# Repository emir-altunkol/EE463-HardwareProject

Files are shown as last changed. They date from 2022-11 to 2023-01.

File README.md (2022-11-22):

# EE463-HardwareProject

This is a repository for the term project of the EE463 Static Power Conversion I course given by METU EEE department. It is a DC motor drive project, whose details are included in the [course repository](https://github.com/odtu/ee463).

## Team Members (Hard-Time Regulators): 

* Işık Emir Altunkol
* Fatih Erden
* İsmail Macit

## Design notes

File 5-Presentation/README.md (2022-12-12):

## Component List

The spreadsheet link for the current state of the component list is given [here](https://docs.google.com/spreadsheets/d/14lQKjTt1QYeIo84nUDRivLAAxynFq0hbY2szFumdkH8/edit?usp=sharing).

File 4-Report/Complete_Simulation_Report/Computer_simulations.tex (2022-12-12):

\section{Computer Simulations} \label{simulations}

\subsection{LTspice Simulations}
Since the 4-quadrant operation and control of the H-Bridge topology is not simple, we made comprehensive simulations using LTspice.A brief description of those and their results will be explained in this subsection. First, the simulation model will be described. \\

The model for the topology we are using is given in Figure \ref{fig:LTspice_topology_sch}. MOSFET models are chosen from the libraries of LTspice, whose ratings are compatible with our operation ranges. To simulate the rectified DC voltage on the input side, we occasionally used an ideal DC source to simplify the results by avoiding the input voltage ripple. We used a diode to model the one-directional current flow of the rectifier, and a capacitor to model the output filtering capacitor of the rectifier. The chopper and the H-Bridge is model is rather straightforward.

\begin{figure}[H]
    \centering
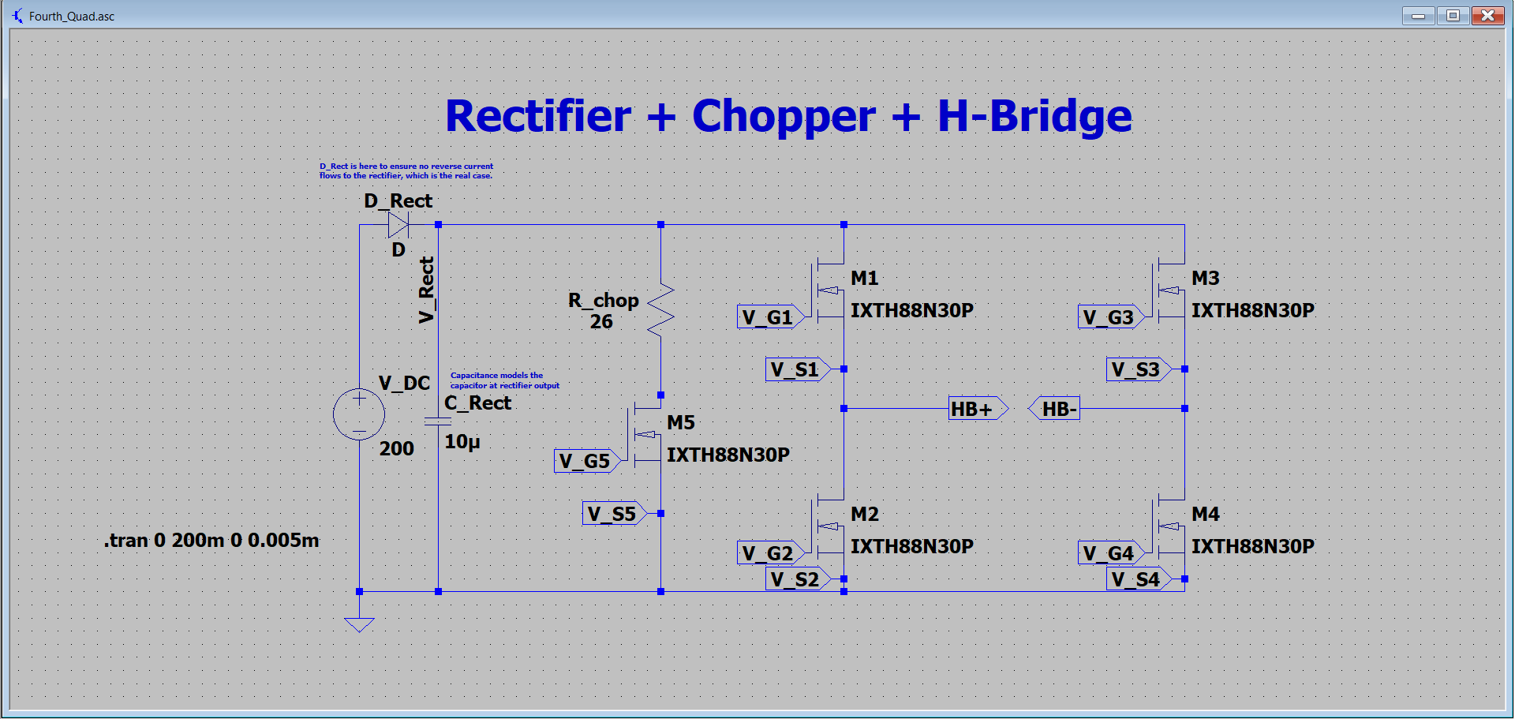
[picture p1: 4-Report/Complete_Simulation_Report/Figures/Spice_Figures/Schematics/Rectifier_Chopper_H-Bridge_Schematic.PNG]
    
    \caption{Simulation model for the 4-quadrant motor driver topology we choose}
    \label{fig:LTspice_topology_sch}
\end{figure}

The controller and gate driver sections in Figure \ref{fig:LTspice_driver_controller_sch} are modeled using behavioral and usual voltage sources to create the necessary gate to source voltages.

\begin{figure}[H]
    \centering
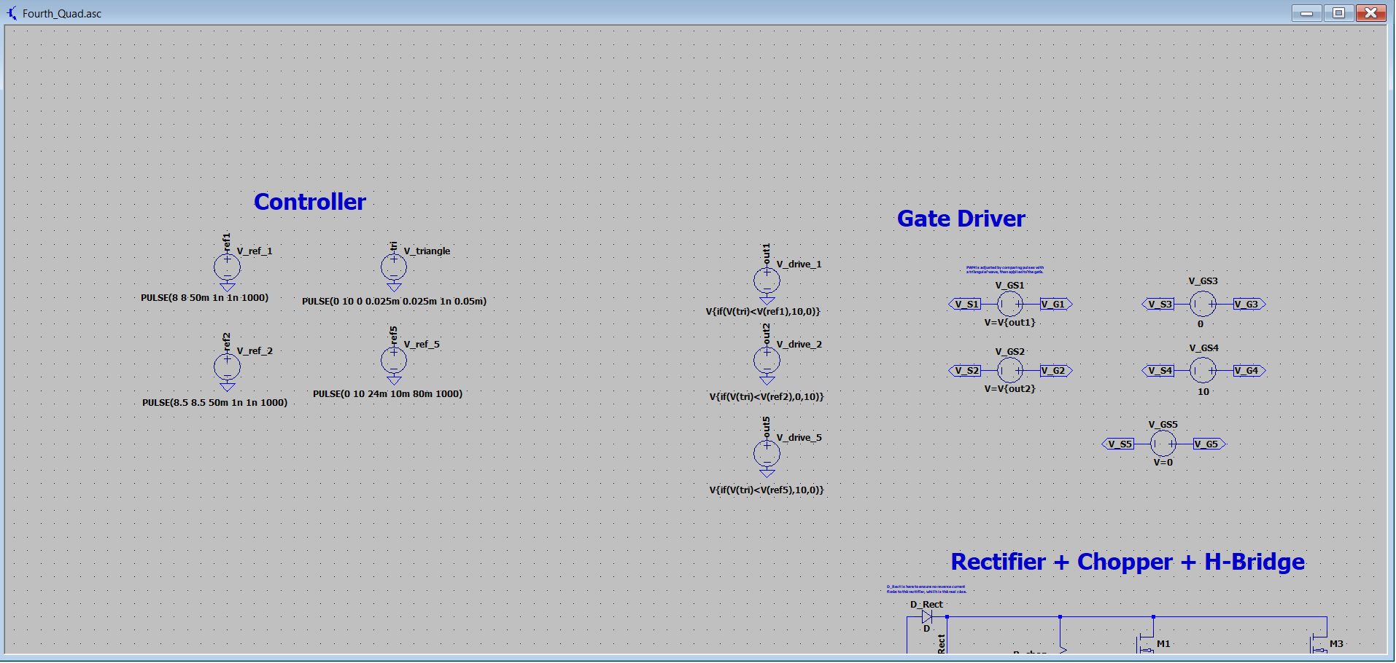
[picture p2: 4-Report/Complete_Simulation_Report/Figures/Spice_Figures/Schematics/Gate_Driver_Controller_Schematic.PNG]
    
    \caption{A simple model to simulate the gate driver and controller operation}
    \label{fig:LTspice_driver_controller_sch}
\end{figure}

The electromechanical simulation models for DC motors are given in Figure \ref{fig:LTspice_motor_sch}. Since the simple model of the DC motor is also LTI (Linear Time Invariant), we can simulate it using the LTI circuit which is built and shown in the figure. The model can be derived using the mechanical laws for rotational systems, the torque and back emf formulas of the DC motor models, and Kirchoff's circuital laws. The motor parameters are not the final values, but found iteratively to simulate the DC motor we used as realistically as possible. Note that another DC machine is coupled to our DC machine which is going to be the The overall model for the LTspice simulations is given in Figure \ref{fig:LTspice_whole_sch}.

\begin{figure}[H]
    \centering
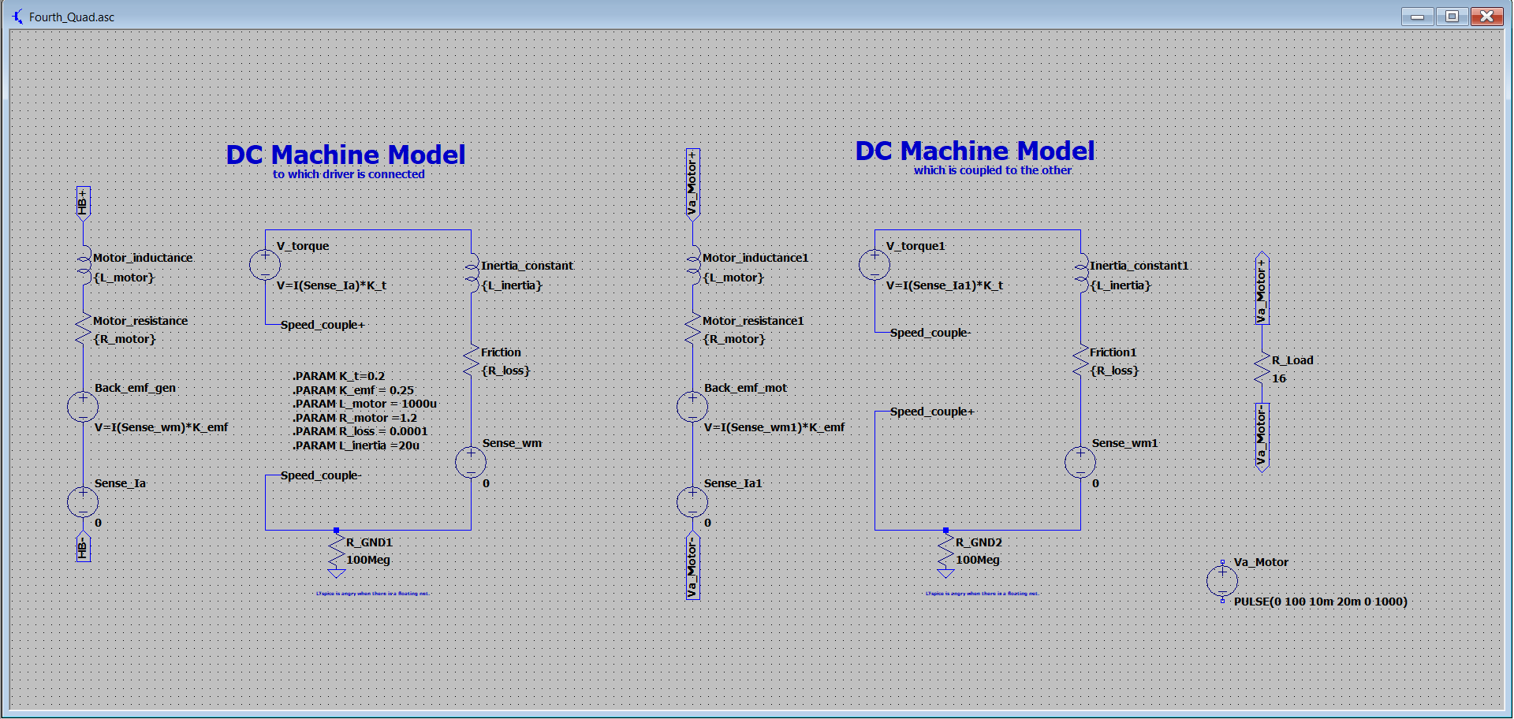
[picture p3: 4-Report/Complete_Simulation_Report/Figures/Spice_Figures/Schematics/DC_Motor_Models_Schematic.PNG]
    
    \caption{Electromechanical simulation model for DC motors}
    \label{fig:LTspice_motor_sch}
\end{figure}

\begin{figure}[H]
    \centering
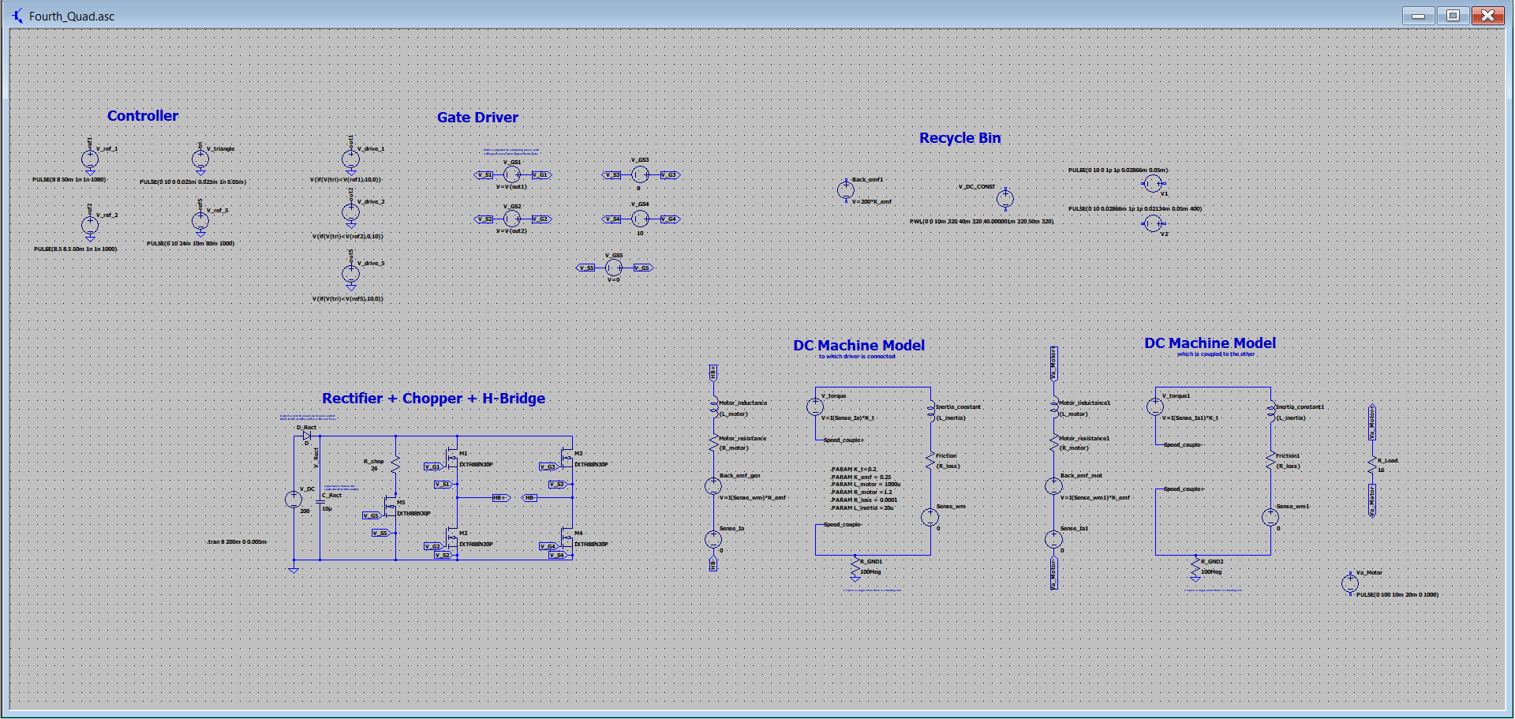
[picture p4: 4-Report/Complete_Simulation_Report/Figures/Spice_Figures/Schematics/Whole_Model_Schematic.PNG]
    
    \caption{The complete simulation model used for the DC motor drive simulations in LTspice}
    \label{fig:LTspice_whole_sch}
\end{figure}

For the forward motoring region simulations, M1 and M2 MOSFETs are used for switching, M3 is always off, and M4 is always on for H-Bridge to operate as a synchronous buck converter. The output voltage level is directly proportional with the duty cycle of M1. For example, for 90\% duty, we obtain 180V average voltage on the motor terminals, and we obtain 100V for 50\% duty. These cases are simulated and shown in Figures \ref{fig:LTspice_forward_90_duty} and \ref{fig:LTspice_forward_50_duty}. The current on the 16 $\Omega$ load, the armature current, and the voltage on the H-Bridge terminals are given in the figures. Note that for these values, one can supply more than 2kW power with the motor driver. Hence, current and voltage ratings of the MOSFETs can be determined using such a simulation (keeping the other practical effects in mind).

\begin{figure}[H]
    \centering
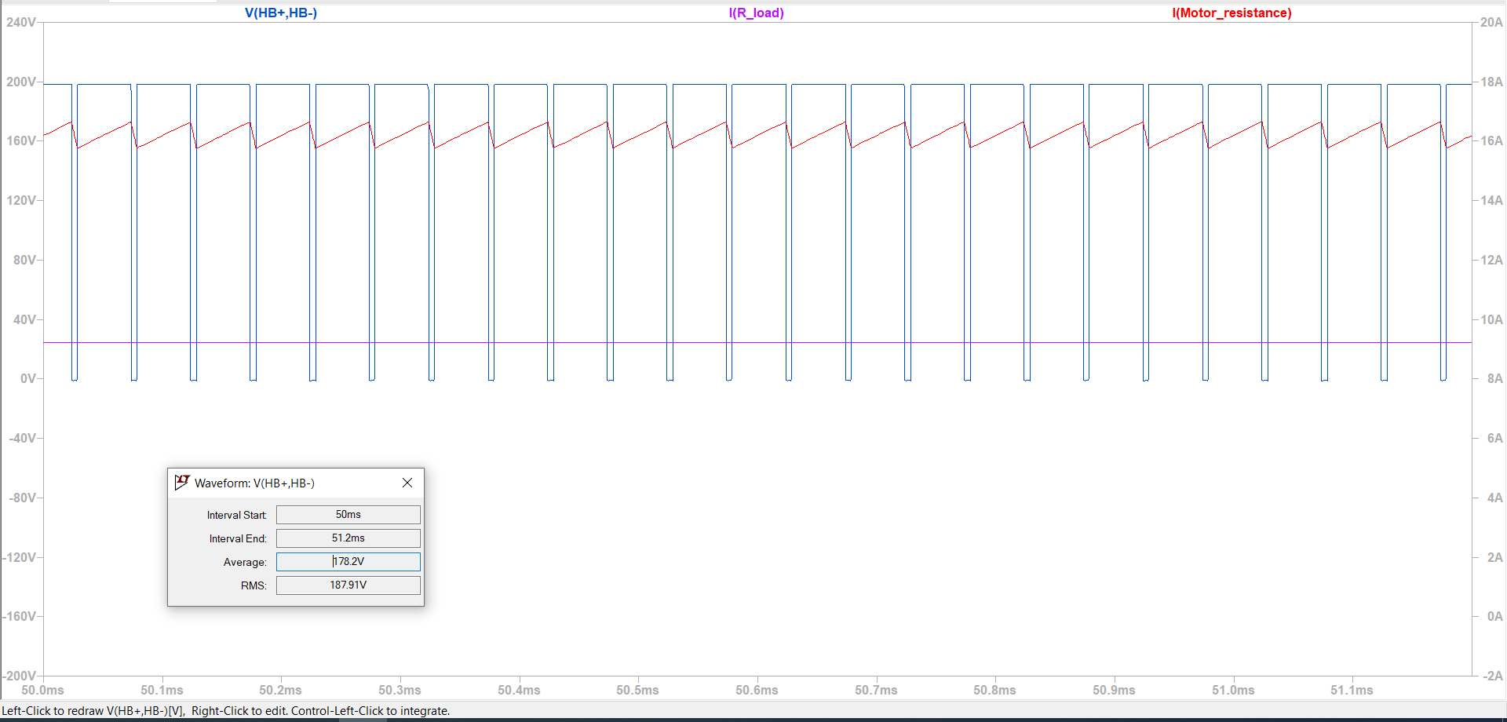
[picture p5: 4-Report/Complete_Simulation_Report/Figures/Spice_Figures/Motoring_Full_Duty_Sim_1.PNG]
    
    \caption{Forward motoring simulation for 90\% duty}
    \label{fig:LTspice_forward_90_duty}
\end{figure}

\begin{figure}[H]
    \centering
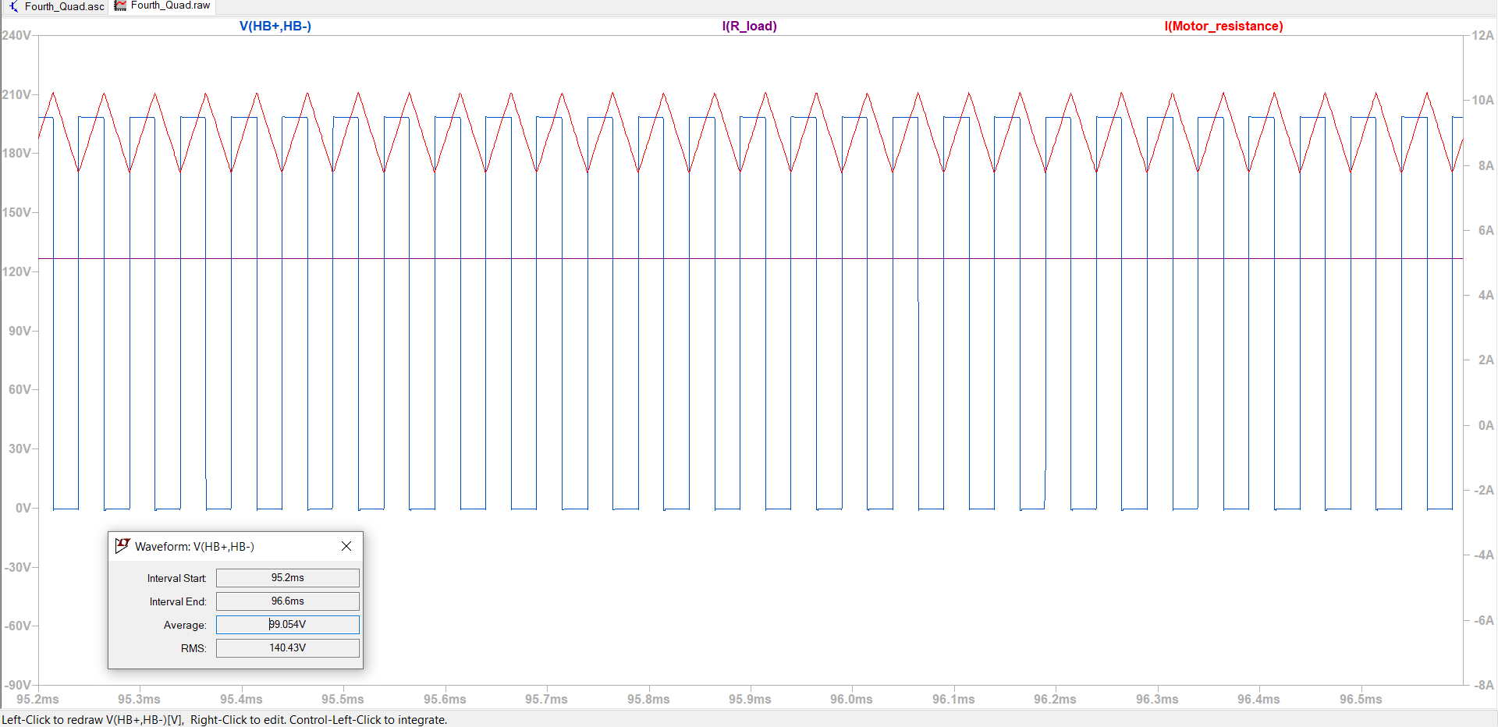
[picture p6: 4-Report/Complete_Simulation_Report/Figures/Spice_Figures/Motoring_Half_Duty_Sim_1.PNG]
    
    \caption{Forward motoring simulation for 50\% duty}
    \label{fig:LTspice_forward_50_duty}
\end{figure}

All these simulations are also done with a rectified input, which is coming from a three phase full bridge rectifier. Forward motoring simulation results for the rectified input voltage is given in Figure \ref{fig:LTspice_forward_90_duty_rectified}. Note that there is a significant current ripple in steady state, which is not desired. This will be avoided by the closed loop PID current control by changing the duty according to the input voltage.\\

The average power plots for the output of the driver and one of the switching MOSFETs (M1) are given in Figure \ref{fig:LTspice_forward_90_duty_rectified_power}. The average power consumed by the MOSFET is also calculated and found to be around 10W. This value does not accurately model the real losses, but still gives an idea about the order of magnitude of the MOSFET losses, which is very satisfying for this simulation. In future simulations, more realistic thermal models and simulations will be made.

\begin{figure}[H]
    \centering
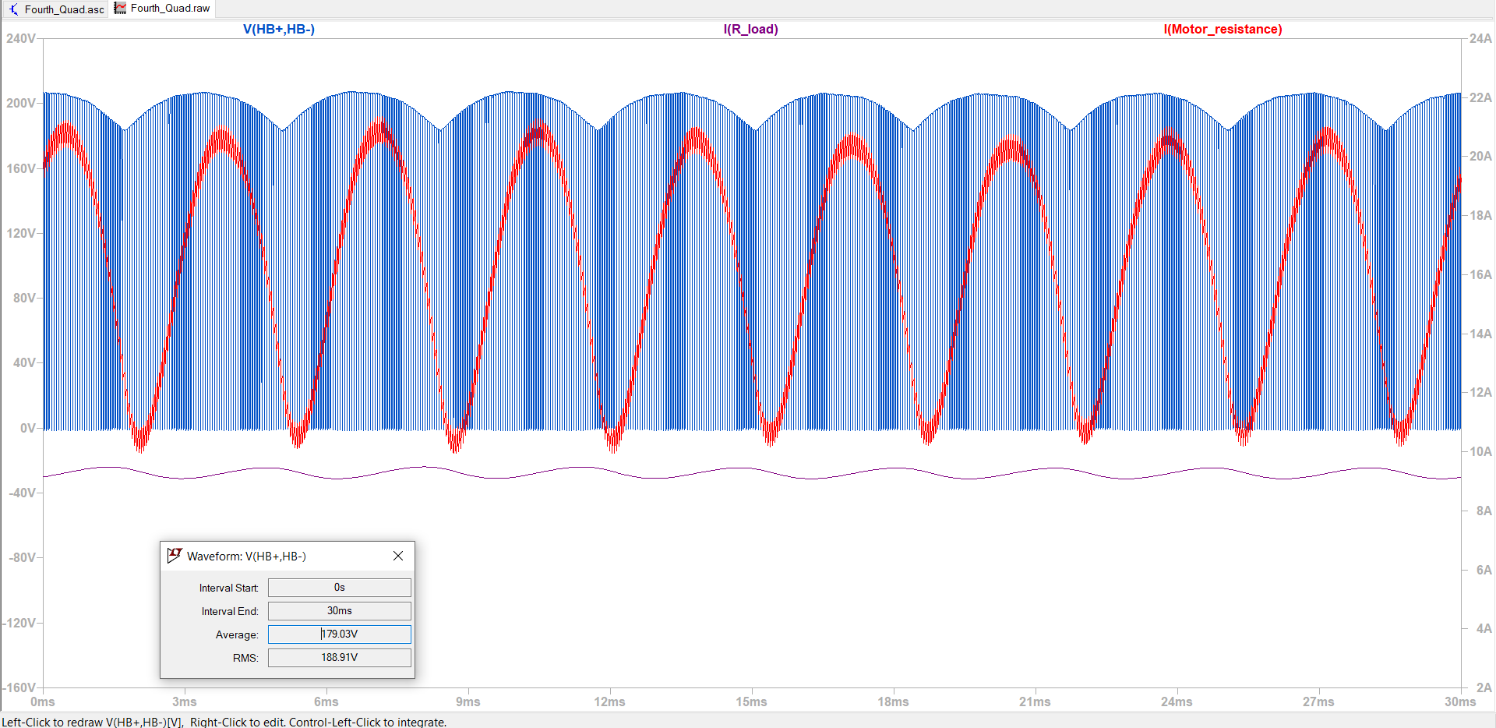
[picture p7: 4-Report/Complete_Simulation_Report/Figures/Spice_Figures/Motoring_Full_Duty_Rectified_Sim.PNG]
    
    \caption{Forward motoring simulation for 90\% duty with rectified input}    \label{fig:LTspice_forward_90_duty_rectified}
\end{figure}

\begin{figure}[H]
    \centering
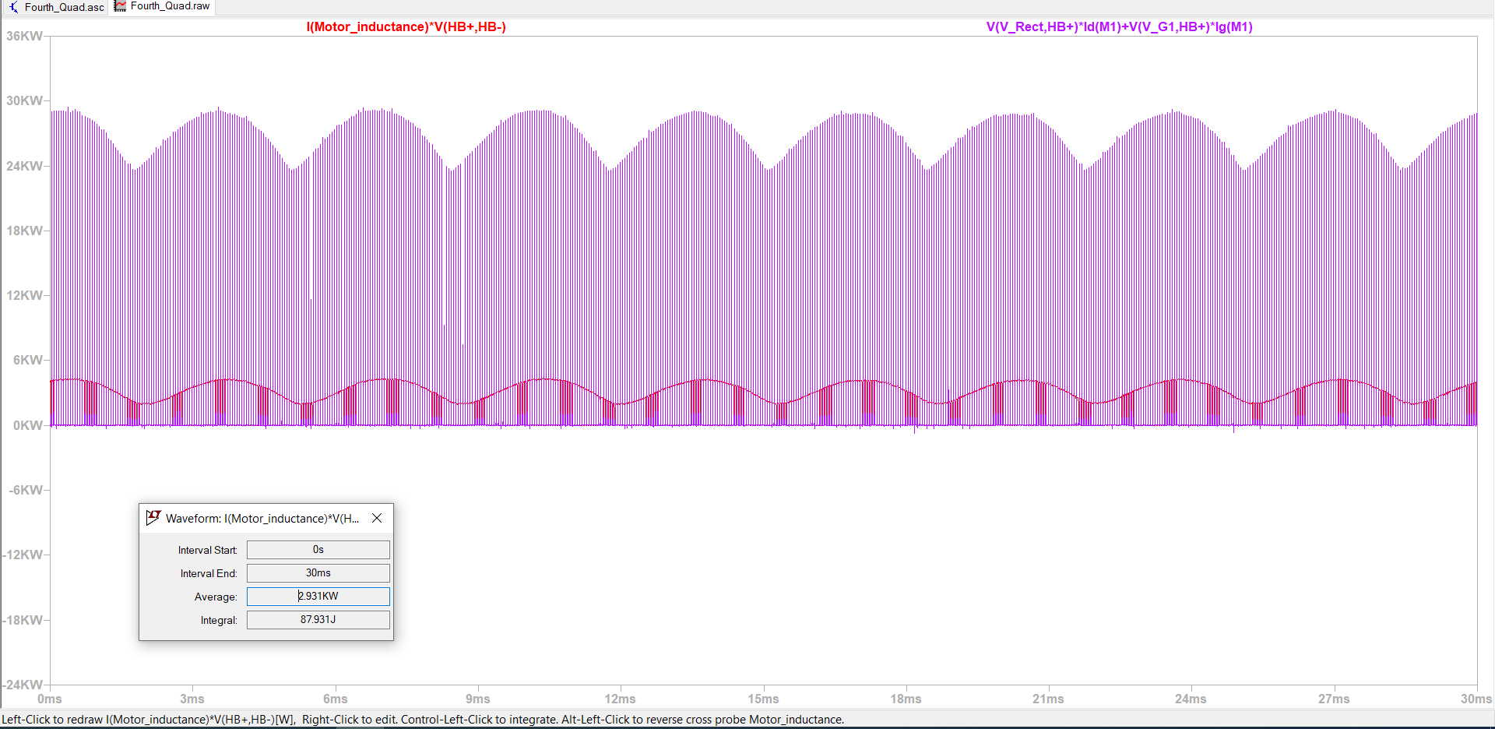
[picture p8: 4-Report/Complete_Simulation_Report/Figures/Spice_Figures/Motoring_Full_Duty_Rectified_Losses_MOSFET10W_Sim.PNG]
    
    \caption{Forward motoring simulation for 90\% duty with rectified input, power plots}
    \label{fig:LTspice_forward_90_duty_rectified_power}
\end{figure}

For testing both the forward motoring and regenerative breaking, we made a simulation in which we suddenly change the duty from 90\% to 50\%. This will try to slow down the motor and the motor will release its dissipate its kinetic energy by supplying power to the driver. At this moment, since we did not switch on the chopper resistor in the simulation, the capacitor on the input side is charged to a large value. The transient response is seen in Figure \ref{fig:LTspice_regenerative_breaking}. Note that when our current sensor senses the reverse current, the micro-controller will switch the chopper resistor on and the energy will be dissipated on the resistor.

\begin{figure}[H]
    \centering
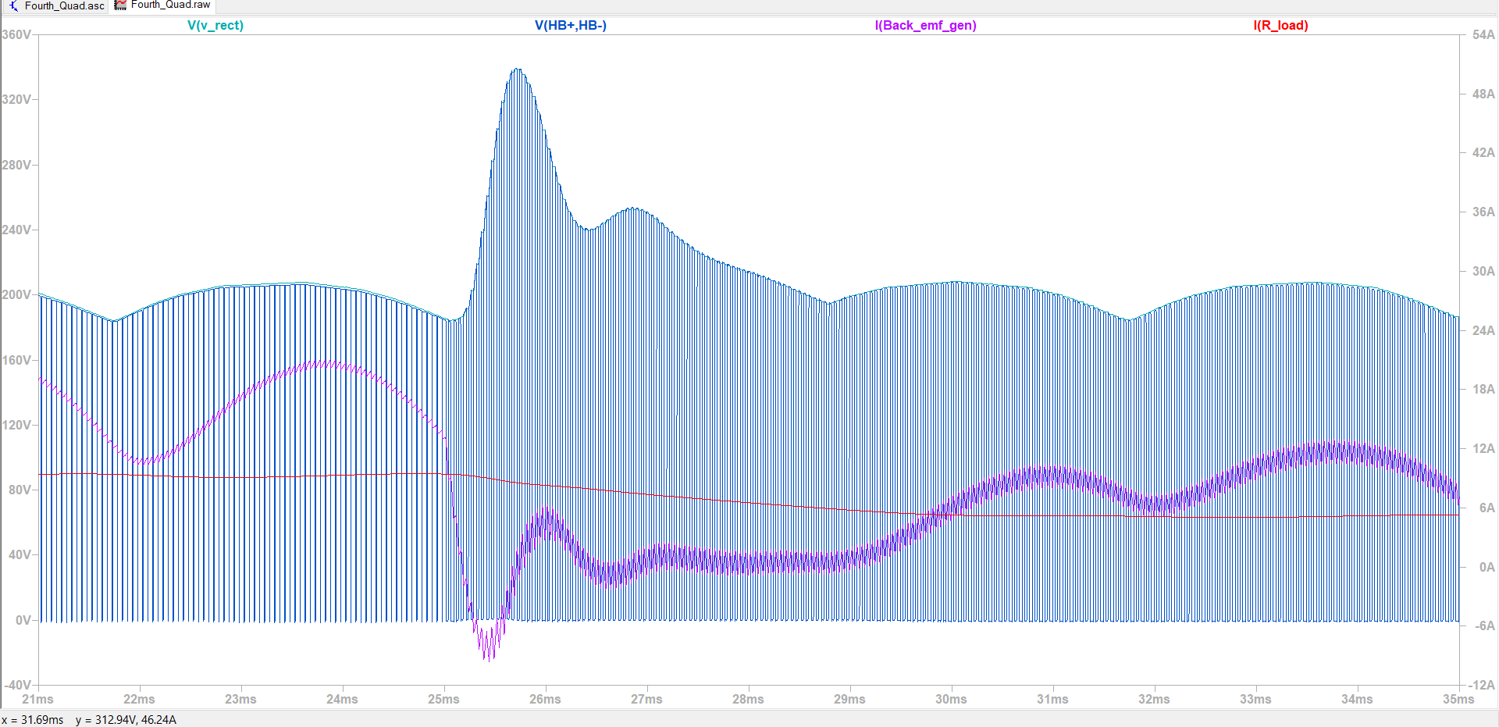
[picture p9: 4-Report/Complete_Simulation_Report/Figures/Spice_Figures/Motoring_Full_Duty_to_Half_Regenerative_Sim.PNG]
    
    \caption{Regenerative breaking simulation for sudden slow down (transient)}    
    \label{fig:LTspice_regenerative_breaking}
\end{figure}

The same simulations are run for the reverse motoring operation (M1 off, M2 on, M3 and M4 switched for a synchronous buck with inverted output voltage). The results were similar to the forward motoring case, except for the directions of the currents and voltages on the armature side, which was expected. \\

Finally, the continuous operation in the generation mode is tested by supplying a higher voltage to the other motor. In this operation, none of the MOSFETs are switched on except the chopper switch. The current flow is permitted by the body diodes of the MOSFETs. In the real case, M1 and M4 can be switched to increase the efficiency, but no need to simulate that case. Chopper MOSFET is switched on after 1ms the other motor starts to rotate. The simulation results are given in Figure \ref{fig:LTspice_generation}. One can see that the armature current is negative after the transient, hence supplied to the driver; and the chopper current is positive. These are the desired transient and steady responses of the generation mode and the results are as expected. \\

\begin{figure}[H]
    \centering
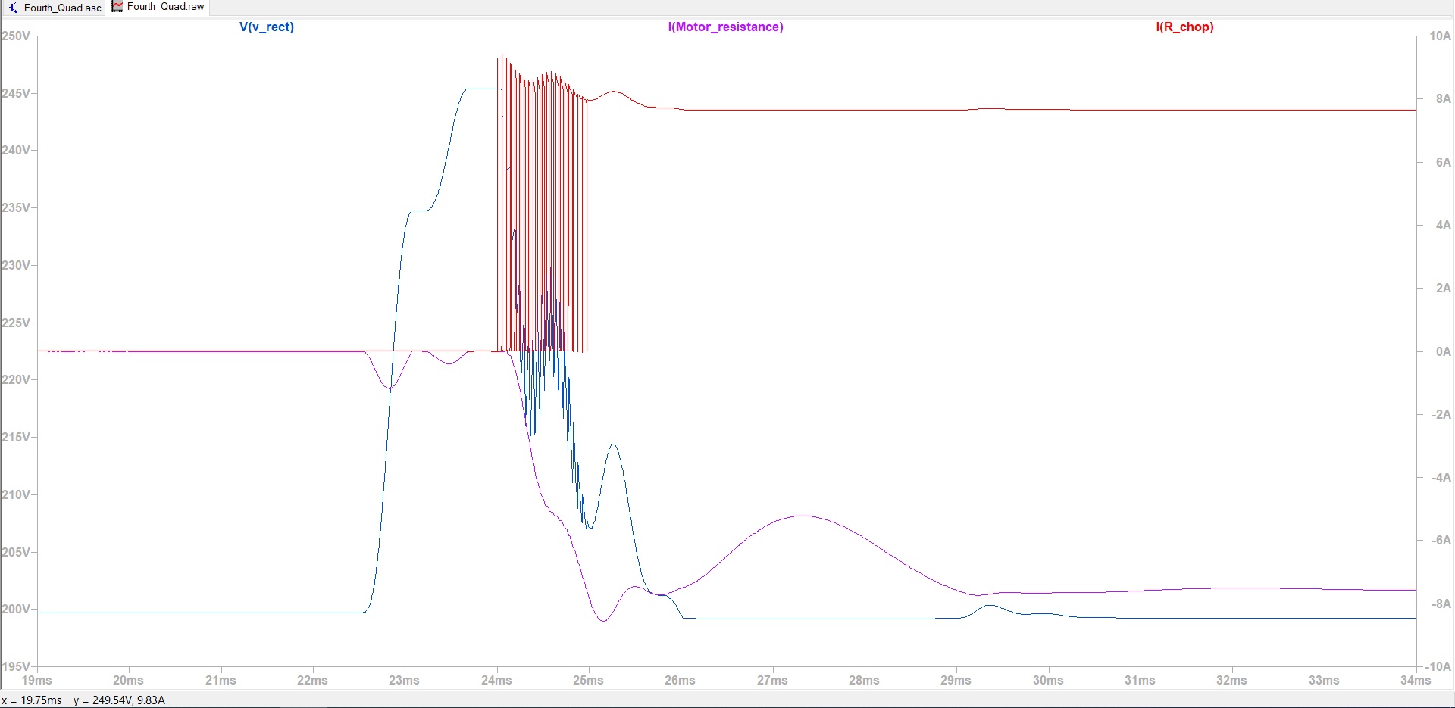
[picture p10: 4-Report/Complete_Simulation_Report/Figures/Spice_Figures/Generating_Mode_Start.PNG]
    
    \caption{Continuous generation mode simulation}   
    \label{fig:LTspice_generation}
\end{figure}

In the next steps, we need to consider the inductances and resistances caused by the copper tracks of the PCB layout, which will cause unwanted effects. The realistic models of the components we choose will also be included in the simulations to get better results. Finally, thermal simulations will be conducted according to the directives given by the component manufacturers to further investigate the thermal properties of the system. We continuously update and iterate our simulations to obtain a better view of the electrical, thermal, and mechanical systems considered in our project. For now, we have seen that using H-Bridge topology, we can operate our DC motor in all 4-quadrants with great success.

\subsection{MATLAB Simulations}
Expected circuitry is simulated using MATLAB/Simulink environment. The first stage is added as a three-phase full-bridge rectifier. After that H-bridge and motor simulations are added to have a complete simulation. Simulation setup can be seen in Figures \ref{fig:matlab_model1} \&
\ref{fig:matlab_model2}.

\begin{figure}[ht]
    \centering
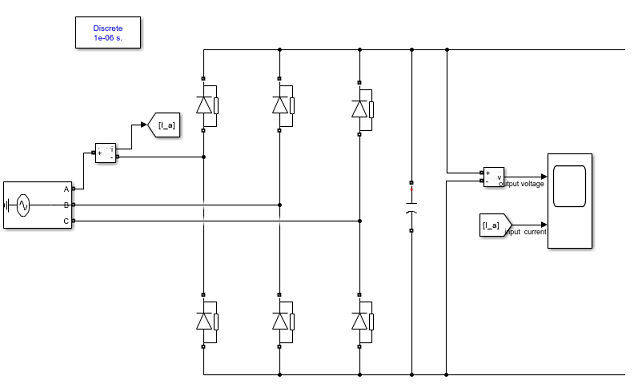
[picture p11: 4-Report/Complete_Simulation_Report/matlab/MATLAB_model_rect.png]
    
    \caption{MATLAB Simulation Model Three-Phase FBDR.}
    \label{fig:matlab_model1}
\end{figure}

\begin{figure}[ht]
    \centering
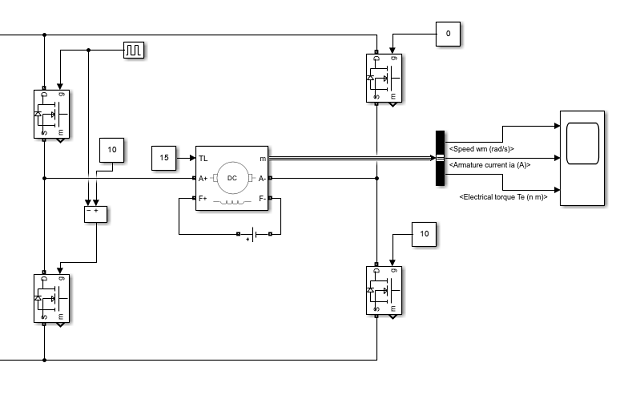
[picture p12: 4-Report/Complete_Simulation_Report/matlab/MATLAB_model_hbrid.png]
    
    \caption{MATLAB Simulation Model H-Bridge}
    \label{fig:matlab_model2}
\end{figure}

In this simulation setup, phase-to-phase voltages are given as 150 $V_{rms}$. The output is around 200 $V_{rms}$ with 20 $V_{pp}$ ripple. The H-bridge and DC motor are driven with the output of a three-phase full bridge diode rectifier. Separate simulations are run for motoring, reverse motoring, and regenerative braking modes of operation. In forward motoring, the system works as a synchronous DC-DC buck converter. The output of the forward motoring can be seen in the 50 percent duty cycle in Figure \ref{fig:forward_mot}. The output current is observed to be too much for the system. This is because there is no soft starter simulated. The control part will be implemented later.

\begin{figure}[ht]
    \centering
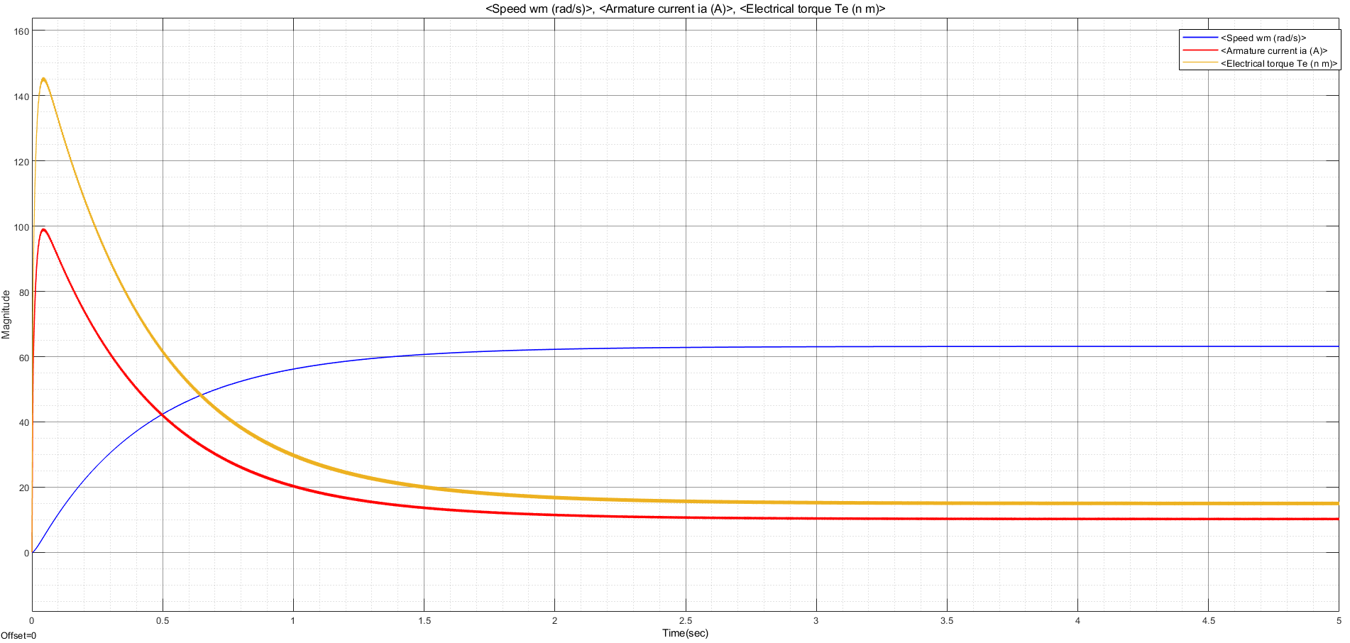
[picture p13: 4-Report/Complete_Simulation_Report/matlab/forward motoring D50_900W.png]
    
    \caption{H-Bridge and DC Motor Simulation at D=0.5 - Forward Motoring}
    \label{fig:forward_mot}
\end{figure}

In Figure \ref{fig:rev_mot}, we see the reverse motoring graph of the motor. It is just the inverted version of forward motoring. The system works with the same logic; however, the controlled MOSFETs are changed due to change of operation. 
\begin{figure}[ht]
    \centering
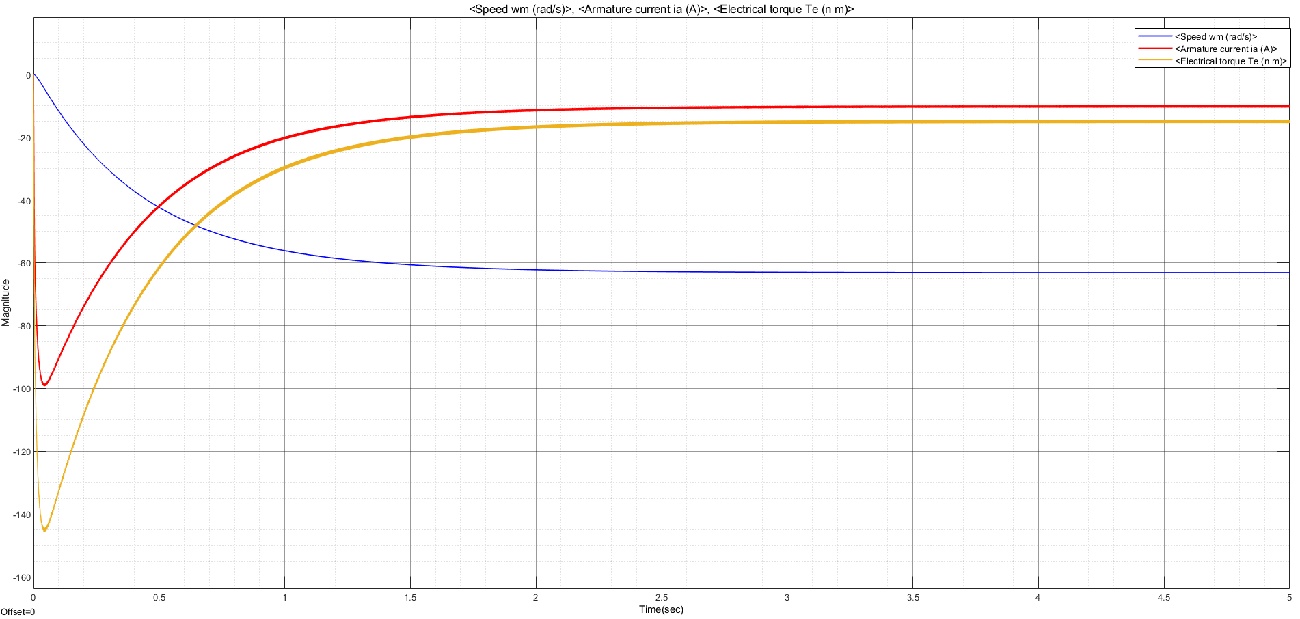
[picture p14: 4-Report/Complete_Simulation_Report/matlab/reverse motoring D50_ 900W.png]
    
    \caption{H-Bridge and DC Motor Simulation at D=0.5 - Reverse Motoring}
    \label{fig:rev_mot}
\end{figure}

The intention of using an H-bridge is to be able to have the four-quadrant drive. More on that topic is explained in Design Decisions[\ref{design}]. The other operation quadrants are braking regions. Braking is simulated in the model by adding a resistor and another MOSFET parallel to the rectifier output as in Figure \ref{fig:braking}.
\newpage
\begin{figure}[ht]
    \centering
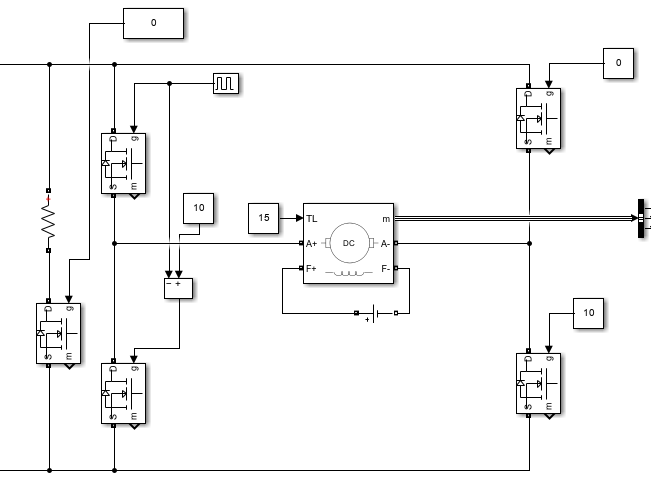
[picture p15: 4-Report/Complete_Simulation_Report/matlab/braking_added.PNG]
    
    \caption{Braking Mode Added Circuitry}
    \label{fig:braking}
\end{figure}

In regenerative braking, the intention is usually to charge a battery system connected to the motor. We will dissipate this external motor energy using a chopper resistor. When it is in braking mode we turn on our MOSFET. More on the operation of the braking mode is explained in Design Decisions[see \ref{design}].

Figure \ref{fig:duty_braking} shows that the current gets below zero, which means our motor injects current into the other direction. This change in the current increases the voltage if not dissipated properly.
\begin{figure}[ht]
    \centering
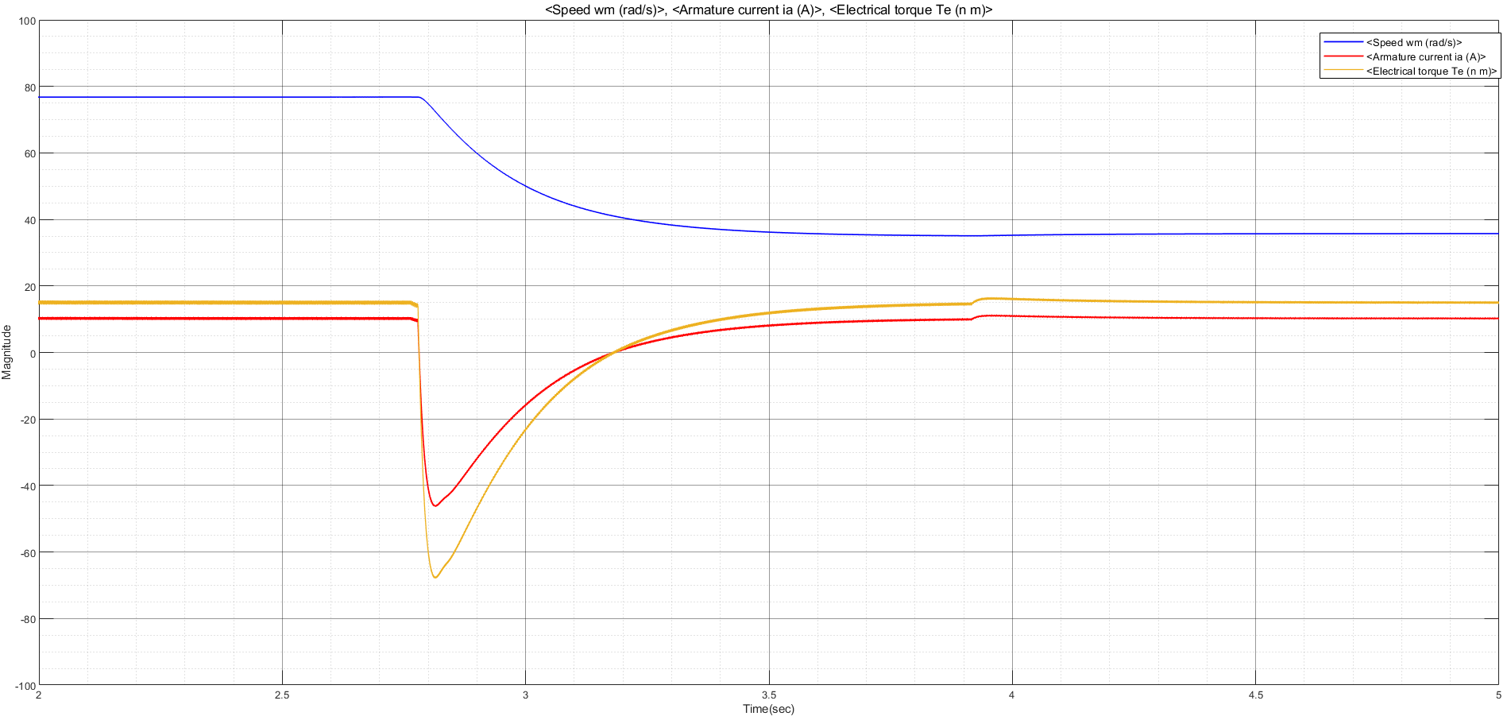
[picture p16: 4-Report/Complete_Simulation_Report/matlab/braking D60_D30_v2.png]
    
    \caption{Forward Braking from duty cycle D=0.6 to D=0.3 }
    \label{fig:duty_braking}
\end{figure}

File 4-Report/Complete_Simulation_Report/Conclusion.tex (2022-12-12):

\section{Conclusion} \label{conclude}

In this report, the first analysis of the selected design for the DC-motor drive, is performed. For the achievement of 4 quadrant operation and ease of control, full-bridge diode rectifier and H-bridge is selected as the design topology. The selected design is compared with other possible topologies for the task based on its advantages and theoretical performances. Simulation of the individual modules are done with some of the non-idealities being present in the simulations. According to the simulation results, rated voltage and current values for different modes of operations, are detected for the components to be implemented in real life application. Appropriate and commercially available diodes, MOSFETs and capacitors are selected for the implementation step of the project.

In the next steps of the project, the most suitable and commercially available ones from the selected models (also new models found recently in the further market research), will be bought. After checking the detailed simulation of these models (including non-idealities of the models to the simulation as much as possible), the implementation phase will start and considering the project specifications, design deliverables and test requirements, design will be modified until the end of the implementation phase of the project.

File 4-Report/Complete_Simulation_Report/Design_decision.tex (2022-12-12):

\section{Design Decisions} \label{design}
In this section, comparison of different topologies and the decision process of our team are given. The advantages of the selected topology, reasons behind it, possible difficulties that can occur during the process are discussed. Controlling of the selected topology and signal and interactions between the modules of the design are explained in the following subsection. Then mechanical and thermal issues of the design are discussed. Possible solutions to the stability and heating problems of the design are proposed. Finally connection and measurement ports of the device for application and testing are discussed. 

\subsection{Topology Selection}

There are common topologies like thyristor rectifiers (three-phase or single-phase) for rectifying AC input and controlling the DC-output at the same time. By controlling the firing angles ($\alpha$) of the thyristors, one can adjust the voltage levels of the output voltage. A topology given in Figure \ref{fig:single_phase_thyristor_fb} is an example to this topology. As it can be seen in the figure, 4 thyristors are to be controlled with their $\alpha$ firing angles. In three-phase case of the same topology, this 6 thyristors are to be controlled. However, this configuration does not support 4 quadrant operation of the DC motor since the thyristors allow only way for the current to flow. To achieve the 4 quadrant operation, one can replace each thyristor with back-to-back two thyristors, which can be seen in Figure \ref{fig:triac}. Control of this configuration is again more complex. \\

\begin{figure}[H]
    \centering
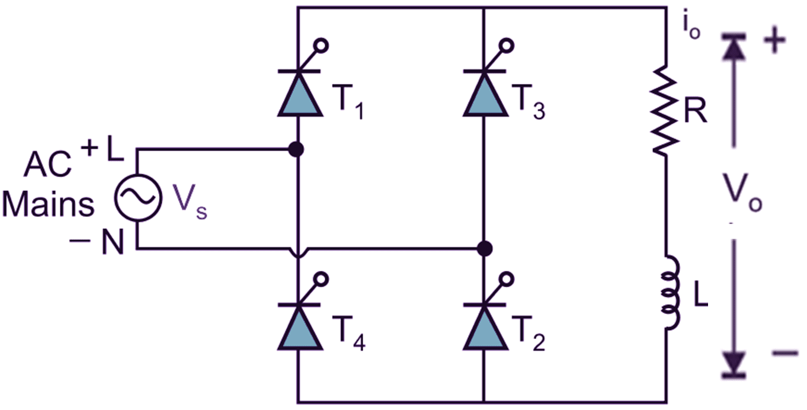
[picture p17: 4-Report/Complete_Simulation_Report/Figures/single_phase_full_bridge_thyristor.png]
    
    \caption{Single-phase full bridge thyristor rectifier.}
    \label{fig:single_phase_thyristor_fb}
\end{figure}

\begin{figure}[H]
    \centering
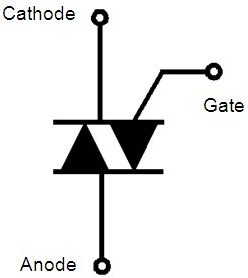
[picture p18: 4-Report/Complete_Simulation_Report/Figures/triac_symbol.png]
    
    \caption{Back-to-back thyristors (triac).}
    \label{fig:triac}
\end{figure}

One can also use a diode rectifier (3-phase or single phase) before the DC-DC converter. In second case, only the DC-DC converter is controlled for the output voltage level. Since the maximum value of the desired output DC voltage is 180 V, a buck converter will be suitable for this case. However this topology works only in one quadrant due to the unavailability of negative duty cycles and one way allowance of the diode. To achieve the 4-quadrant operation, one alternative is the H-bridge coming after the diode rectifier. By adjusting the duty cycles of appropriate switches for desired quadrant of operation, one can drive the DC motor in all regions. Our motor drive will be designed to support 4-quadrant operation. Therefore, the topology which includes full-bridge diode rectifiers and H-bridge controller is selected to be implemented. Overall configuration of the design that will drive the DC motor is given in the Figure \ref{fig:overall_diagram}. In generation modes, armature current flowing to the driver will be dissapated through a chopper resistance which is also controlled by a switch to utilize its operation. \\

\subsection{Control Methodology}
We will use PWM (Pulse Width Modulation) signals to control the MOSFETs, which will control the average voltage seen in the output terminals. We will use a micro-controller to generate and regulate the PWM signals according to the user input and system state. To drive the MOSFETs with the micro-controller signals, we need to use gate driver circuits. We will use an Arduino controller (ATMegaxxx) as microcontroller, and commercial half-bridge gate drivers will be ordered and used directly to reduce the circuit design workload and have better performance. \\

To be able to soft-start the DC-motor, avoid the armature current ripple, and avoid high transient currents during reference input changes, we will need a closed loop control methodology between DC-motor terminal voltage and the duty cycles of the switches (MOSFETs). If we do not control the terminal voltage and apply PWMs with constant duty cycles, motor will experience huge amount of torques (inducing high currents on the armature) that will damage the DC-motor and decrease its lifetime. Figure \ref{fig:overall_diagram} shows the overall control topology of the DC-motor driver design. Overall, the design does not control the rectifier side of the motor drive, full-bridge diode rectifiers are used to rectify the AC input. Then the ripple at the DC-output will be suppressed by an appropriate shunt capacitor. To be able drive the DC-motor on the generating modes, team decided not to supply the energy to the grid side, since the design does not have an inverter that will generate AC to be supplied to the grid. Instead, there will be open terminals for chopper resistance that will dissipate the supplied power when the DC-machine operates in generating modes. And then, depending on the operation mode, the controller will send the required PWM duty cycles to the gate drivers of the switches. Detailed information about the closed loop controls of switches are given below.

\begin{figure}[H]
    \centering
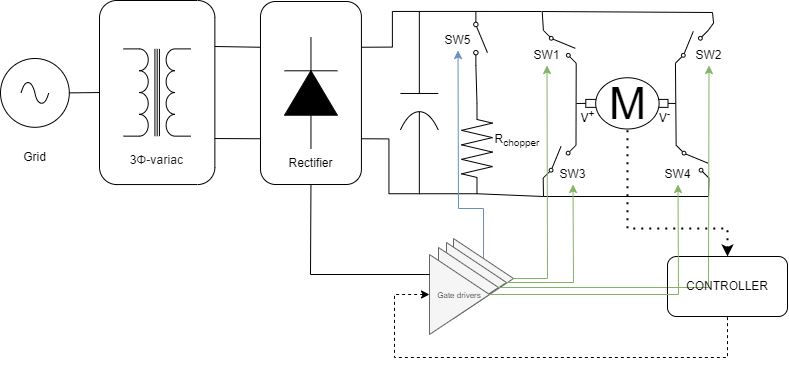
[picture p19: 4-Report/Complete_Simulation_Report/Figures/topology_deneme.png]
    
    \caption{DC-motor drive system diagram.}
    \label{fig:overall_diagram}
\end{figure}

In our design, we plan to use closed-loop current control to control our driver by implementing a PID (Proportional Integral Derivative) controller. Since the armature current increases with increasing duty, it can be controlled by changing the duty cycles of the switches. The duty cycles will be adjusted using an error signal. By taking the discrete time derivative and integral of this error signal, we may obtain a discrete time PID controller. The equation for controlling the current by adjusting the duty cycle is given in Equation \ref{eqn:PID}.

\begin{equation}
    \begin{split}
        \Delta D = K_pE_{I_a} + K_i\sum_{n=1}^{t} E_{I_a}\Delta t + K_d\frac{\Delta E_{I_a}}{\Delta t}
    \end{split}
    \label{eqn:PID}
\end{equation}
\\
\subsection{Mechanical, Thermal, and Isolation Considerations}

In order to protect the DC-motor driver design from external incidents and achieve safer operation for users, the design will be enclosed in a 3D printed box. The size and shape of the box will be appropriate for industrial design applications. According the component sizes and PCB dimensions, smallest box volume will be selected and the DC-motor drive will be fixed in the volume. \\

Placement and connections of the components of the DC-motor drive will be solved on the PCB. This will prevent possible human-made errors and resulting parasitic effects on the circuit. It will also ease the industrial production of the design. \\

After the component selection and their trials during the implementation process, the conduction and switching losses will be calculated, compared with their simulation counterparts, then a proper-sized heatsink will be placed where the most of the heat losses occur on the circuit. \\

To prevent the motor driver circuit from possible loops that will endanger the operation of components, some isolation is required between the power flow lines and signal lines of the circuit and gate drivers. Therefore, the use of optocouplers are to be implemented on the design.

\subsection{Other Considerations}

To make the design available for easy use and proper testing, connection and measurement ports will be added to the design. According to the rated values (current and voltage) of the power lines, required isolation and line thicknesses will be implemented on both the connection ports and the PCB. For input power connection, proper sized banana plugs as seen in Figure \ref{fig:banana} can be selected. According to the connection style of DC-motor to be driven, again proper style of power cables for the output ports, will be selected.

\begin{figure}
    \centering
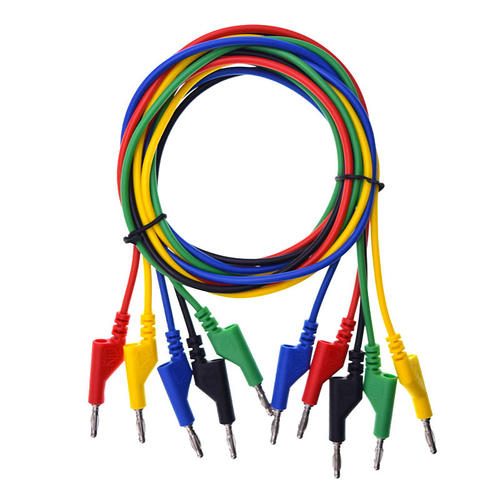
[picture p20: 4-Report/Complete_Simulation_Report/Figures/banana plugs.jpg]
    
    \caption{Banana plug power cables for input side.}
    \label{fig:banana}
\end{figure}

For the measurement ports, the information on test procedures will be requested. Already selected ports for measurements are input and output voltages, ground connection of the motor drive. Since a series connection is requested for the electrical power calculations, it is assumed that power measurements will be taken before the input and output connections. If it is requested, the measurement ports for PWM signals of the gate drivers can be brought into the open. \\

To protect the components from over-voltages and over-currents during the operation, below measures can be applied to the design:

\begin{itemize}
    \item Fuses or current sensors at both the input and output sides of the driver circuit is thought to be implemented for over-current protection. If current sensors are to be implemented on the design, some alarm signal is to be presented to the user through some led or control method can be implemented to cut the power of the circuit.
    \item Since we are asked to supply around 2 kW power through the motor driver (excluding losses), we are dealing with high levels of current and power that can be harmful to a human body. Therefore, proper insulation will be placed on the power lines, ports, and around the equipment.
    \item To cancel the parasitic effects of the non-idealities of the components, proper countermeasures will be considered.
\end{itemize}

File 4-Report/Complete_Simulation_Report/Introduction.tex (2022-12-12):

\section{Introduction} \label{intro}

Starting of DC motors can be tricky in many applications. Basic modelling of DC motors can be given in following figure and equations:

\begin{figure}[ht!]
    \centering
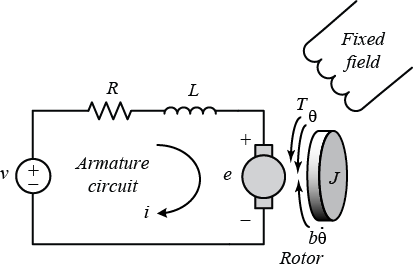
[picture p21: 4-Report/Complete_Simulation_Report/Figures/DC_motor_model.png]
    
    \caption{Simplified DC-machine model.}
    \label{fig:DC-mmotor}
\end{figure}

\begin{equation}
    E_{emf} = K_e\times\omega
\end{equation}

\begin{equation}
    T_e = K_t\times I
\end{equation}

where $K_e$ and $K_t$ are machine constants. $\omega$ being the machine rotational speed, at the starting operation, it is obviously zero. Therefore if we apply a high DC voltage at the starting instant, the DC machine will draw high amounts of currents which can damage the device, permanently. To prevent this possibility, one can start the DC motor in a proper way, not applying a step voltage (rated) to the motor terminals, but rather applying a voltage that increases properly up to the rated value. This kind of operation is called \textit{soft start} and it is helpful  in prolonging the lifetime of the DC motor. In this project, our aim is to make a rectifier controller that is capable of soft-starting the DC motor. Requirements of the controllers and details of the motor of interest are given on course Github web page.\cite{course_git} These will also be used in the following sections of the report.

There are different types of topologies for this purpose of soft start. Some of the common topologies are discussed and evaluated on the issues of efficiency, operation regions and ratings, component availability, thermal and mechanical considerations, etc. on the design decision in \ref{design}. Also, the reasons behind the  design selection of Hard-time Regulators are given in the same section. Selected topology is simulated on computer software programs and the performance of the topology is investigated in the related section \ref{simulations}. Also, possible components that are commercially available and appropriate for the design, are issued on the component selection (see \ref{component}). Summary and future considerations on the design are given in the conclusion.(see \ref{conclude})

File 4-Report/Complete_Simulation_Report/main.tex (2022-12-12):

\documentclass[12pt,a4paper]{article}
\usepackage[pdftex]{graphicx}
\usepackage{url} 
\usepackage[bookmarks, colorlinks=false, pdfborder={0 0 0}, pdftitle={<pdf title here>}, pdfauthor={<author's name here>}, pdfsubject={<subject here>}, pdfkeywords={<keywords here>}]{hyperref} 
\usepackage{caption}
\usepackage{subcaption}
\usepackage{float}
\usepackage{amsmath} % for math and matrix formulations.
\usepackage[section]{placeins}

% Paper margins etc.
\usepackage{geometry}
 \geometry{
 a4paper,
 total={160mm,257mm},
 left=25mm,
 top=25mm
 }

\begin{document}

\input{Title_page}

\pagenumbering{arabic}

\tableofcontents

\newpage
\listoffigures
\listoftables

\newpage
\input{Introduction.tex}

\newpage
\input{Design_decision.tex}

\newpage
\input{Computer_simulations.tex}

\newpage
\input{Component_selection.tex}

\newpage
\input{Conclusion.tex}

\newpage
\bibliographystyle{IEEEtran}
\bibliography{ref.bib}

%\newpage
%\input{Appendix.tex}

\end{document}

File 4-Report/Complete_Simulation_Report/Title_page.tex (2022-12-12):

\begin{titlepage}

\begin{center}

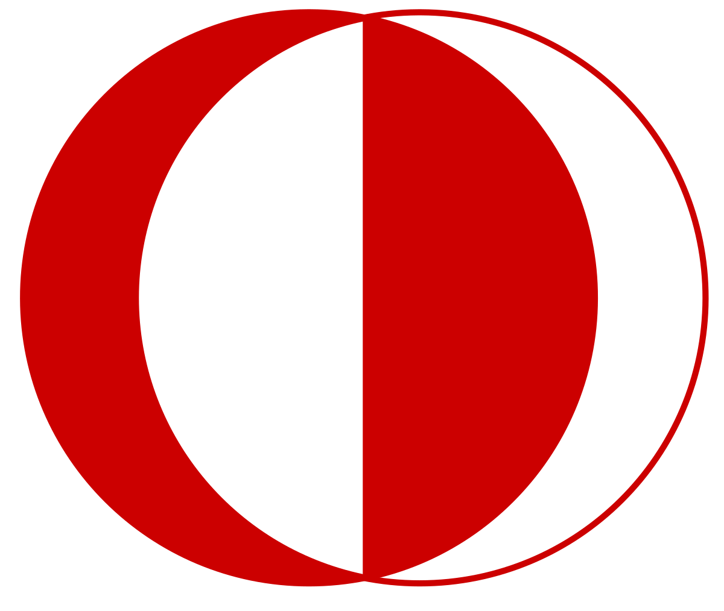
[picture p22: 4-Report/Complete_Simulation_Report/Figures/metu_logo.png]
\\
\vspace{.3in}
\textup{{\bf Middle East Technical University}}\\

% Title
\Large \textbf{EE463 Static Power Conversion I}\\[0.3in]
\Large \textbf{Term Project}\\
\Large \textit{Complete Simulation Report}\\

\noindent\rule{6cm}{0.4pt}

% Authors
\normalsize \textit{Submitted by:} \\

\textbf{Işık Emir Altunkol}\\
\textbf{ID:2442408}\\
emir.altunkol@metu.edu.tr\\
\textbf{tel:531 320 04 43} \\

\vspace{.3in}

\textbf{İsmail Macit}\\
\textbf{ID:2305084}\\
ismail.macit@metu.edu.tr\\
\textbf{tel:539 678 03 96} \\

\vspace{.3in}

\textbf{Fatih Erden}\\
\textbf{ID:}2304566\\
fatih.erden@metu.edu.tr\\
\textbf{tel:} 533 895 38 07\\

\noindent\rule{6cm}{0.4pt}

\vspace{.3in}

\textbf{Submission Date:} 10.12.2022

\end{center}

\end{titlepage}

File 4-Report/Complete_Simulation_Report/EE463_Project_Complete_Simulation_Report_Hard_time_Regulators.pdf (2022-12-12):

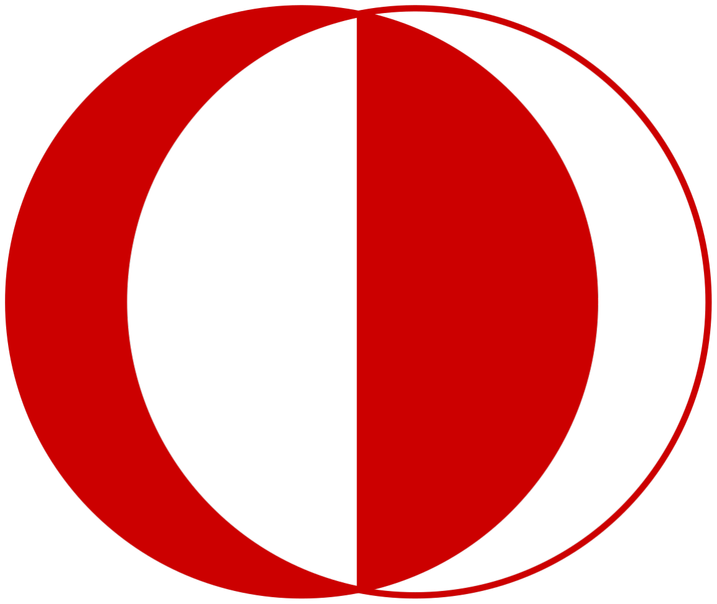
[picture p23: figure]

Middle East Technical University

## EE463 Static Power Conversion I

## Term Project Complete Simulation Report

Submitted by:
I¸sık Emir Altunkol
ID:2442408
emir.altunkol@metu.edu.tr
tel:531 320 04 43

˙Ismail Macit
ID:2305084
ismail.macit@metu.edu.tr
tel:539 678 03 96

Fatih Erden
ID:2304566
fatih.erden@metu.edu.tr
tel: 533 895 38 07

Submission Date: 10.12.2022

## Contents

1 Introduction | 3
2 Design Decisions | 4
3 Computer Simulations | 8
4 Component Selection | 16
5 Conclusion | 17

## List of Figures

1 | Simplified DC-machine model | | 3
2 | Single-phase full bridge thyristor rectifier | | 4
3 | Back-to-back thyristors (triac) | | 4
4 | DC-motor drive system diagram | | 6
5 | Banana plug power cables for input side | | 7
6 | Simulation model for the 4-quadrant motor driver topology we choose . . . | 8
7 | A simple model to simulate the gate driver and controller operation . . . . | 8
8 | Electromechanical simulation model for DC motors | | 9
9 | The complete simulation model used for the DC motor drive simulations
in LTspice | | 9
10 | Forward motoring simulation for 90% duty | 10
11 | Forward motoring simulation for 50% duty | 10
12 | Forward motoring simulation for 90% duty with rectified input | 11
13 | Forward motoring simulation for 90% duty with rectified input, power plots 11
14 | Regenerative breaking simulation for sudden slow down (transient) . . . . 12
15 | Continuous generation mode simulation | 12
16 | MATLAB Simulation Model Three-Phase FBDR | 13
17 | MATLAB Simulation Model H-Bridge | 13
18 | H-Bridge and DC Motor Simulation at D=0.5 - Forward Motoring | 14
19 | H-Bridge and DC Motor Simulation at D=0.5 - Reverse Motoring | 14
20 | Braking Mode Added Circuitry | 15
21 | Forward Braking from duty cycle D=0.6 to D=0.3 | | 15
22 | Three-phase Full Bridge | 16

## List of Tables

1 | Ratings obtained from the Simulations | 16
2 | Ratings obtained from the Simulations | 16
3 | Intended Ratings for MOSFETS | 17
4 | Some of the Selected MOSFETs | 17

## 1 Introduction

Starting of DC motors can be tricky in many applications. Basic modelling of DC motors can be given in following figure and equations:

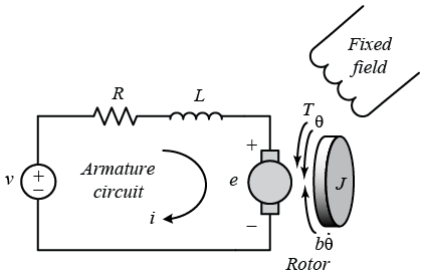
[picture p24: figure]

Figure 1: Simplified DC-machine model.

Eemf = Ke × ω | (1)
Te = Kt × I | (2)

where Ke and Kt are machine constants. ω being the machine rotational speed, at the starting operation, it is obviously zero. Therefore if we apply a high DC voltage at the starting instant, the DC machine will draw high amounts of currents which can damage the device, permanently. To prevent this possibility, one can start the DC motor in a proper way, not applying a step voltage (rated) to the motor terminals, but rather applying a voltage that increases properly up to the rated value. This kind of operation is called soft start and it is helpful in prolonging the lifetime of the DC motor. In this project, our aim is to make a rectifier controller that is capable of soft-starting the DC motor. Requirements of the controllers and details of the motor of interest are given on course Github web page.[1] These will also be used in the following sections of the report. There are different types of topologies for this purpose of soft start. Some of the common topologies are discussed and evaluated on the issues of efficiency, operation regions and ratings, component availability, thermal and mechanical considerations, etc. on the design decision in 2. Also, the reasons behind the design selection of Hard-time Regulators are given in the same section. Selected topology is simulated on computer software programs and the performance of the topology is investigated in the related section 3. Also, possible components that are commercially available and appropriate for the design, are issued on the component selection (see 4). Summary and future considerations on the design are given in the conclusion.(see 5)

## 2 Design Decisions

In this section, comparison of different topologies and the decision process of our team are given. The advantages of the selected topology, reasons behind it, possible difficulties that can occur during the process are discussed. Controlling of the selected topology and signal and interactions between the modules of the design are explained in the following subsection. Then mechanical and thermal issues of the design are discussed. Possible solutions to the stability and heating problems of the design are proposed. Finally connection and measurement ports of the device for application and testing are discussed.

### 2.1 Topology Selection

There are common topologies like thyristor rectifiers (three-phase or single-phase) for rectifying AC input and controlling the DC-output at the same time. By controlling the firing angles (α) of the thyristors, one can adjust the voltage levels of the output voltage. A topology given in Figure 2 is an example to this topology. As it can be seen in the figure, 4 thyristors are to be controlled with their α firing angles. In three-phase case of the same topology, this 6 thyristors are to be controlled. However, this configuration does not support 4 quadrant operation of the DC motor since the thyristors allow only way for the current to flow. To achieve the 4 quadrant operation, one can replace each thyristor with back-to-back two thyristors, which can be seen in Figure 3. Control of this configuration is again more complex.


Figure 2: Single-phase full bridge thyristor rectifier.


Figure 3: Back-to-back thyristors (triac).

One can also use a diode rectifier (3-phase or single phase) before the DC-DC converter. In second case, only the DC-DC converter is controlled for the output voltage level.

Since the maximum value of the desired output DC voltage is 180 V, a buck converter will be suitable for this case. However this topology works only in one quadrant due to the unavailability of negative duty cycles and one way allowance of the diode. To achieve the 4-quadrant operation, one alternative is the H-bridge coming after the diode rectifier. By adjusting the duty cycles of appropriate switches for desired quadrant of operation, one can drive the DC motor in all regions. Our motor drive will be designed to support 4-quadrant operation. Therefore, the topology which includes full-bridge diode rectifiers and H-bridge controller is selected to be implemented. Overall configuration of the design that will drive the DC motor is given in the Figure 4. In generation modes, armature current flowing to the driver will be dissapated through a chopper resistance which is also controlled by a switch to utilize its operation.

### 2.2 Control Methodology

We will use PWM (Pulse Width Modulation) signals to control the MOSFETs, which will control the average voltage seen in the output terminals. We will use a micro-controller to generate and regulate the PWM signals according to the user input and system state. To drive the MOSFETs with the micro-controller signals, we need to use gate driver circuits. We will use an Arduino controller (ATMegaxxx) as microcontroller, and commercial halfbridge gate drivers will be ordered and used directly to reduce the circuit design workload and have better performance.

To be able to soft-start the DC-motor, avoid the armature current ripple, and avoid high transient currents during reference input changes, we will need a closed loop control methodology between DC-motor terminal voltage and the duty cycles of the switches (MOSFETs). If we do not control the terminal voltage and apply PWMs with constant duty cycles, motor will experience huge amount of torques (inducing high currents on the armature) that will damage the DC-motor and decrease its lifetime. Figure 4 shows the overall control topology of the DC-motor driver design. Overall, the design does not control the rectifier side of the motor drive, full-bridge diode rectifiers are used to rectify the AC input. Then the ripple at the DC-output will be suppressed by an appropriate shunt capacitor. To be able drive the DC-motor on the generating modes, team decided not to supply the energy to the grid side, since the design does not have an inverter that will generate AC to be supplied to the grid. Instead, there will be open terminals for chopper resistance that will dissipate the supplied power when the DC-machine operates in generating modes. And then, depending on the operation mode, the controller will send the required PWM duty cycles to the gate drivers of the switches. Detailed information about the closed loop controls of switches are given below.


Figure 4: DC-motor drive system diagram.

In our design, we plan to use closed-loop current control to control our driver by implementing a PID (Proportional Integral Derivative) controller. Since the armature current increases with increasing duty, it can be controlled by changing the duty cycles of the switches. The duty cycles will be adjusted using an error signal. By taking the discrete time derivative and integral of this error signal, we may obtain a discrete time PID controller. The equation for controlling the current by adjusting the duty cycle is given in Equation 3.

∆D = KpEIa + Ki

X

t

n=1

EIa∆t + Kd

∆EIa
∆t

(3)

### 2.3 Mechanical, Thermal, and Isolation Considerations

In order to protect the DC-motor driver design from external incidents and achieve safer operation for users, the design will be enclosed in a 3D printed box. The size and shape of the box will be appropriate for industrial design applications. According the component sizes and PCB dimensions, smallest box volume will be selected and the DC-motor drive will be fixed in the volume.

Placement and connections of the components of the DC-motor drive will be solved on the PCB. This will prevent possible human-made errors and resulting parasitic effects on the circuit. It will also ease the industrial production of the design.

After the component selection and their trials during the implementation process, the conduction and switching losses will be calculated, compared with their simulation counterparts, then a proper-sized heatsink will be placed where the most of the heat losses occur on the circuit.

To prevent the motor driver circuit from possible loops that will endanger the operation of components, some isolation is required between the power flow lines and signal lines of the circuit and gate drivers. Therefore, the use of optocouplers are to be implemented on the design.


Figure 5: Banana plug power cables for input side.

### 2.4 Other Considerations

To make the design available for easy use and proper testing, connection and measurement ports will be added to the design. According to the rated values (current and voltage) of the power lines, required isolation and line thicknesses will be implemented on both the connection ports and the PCB. For input power connection, proper sized banana plugs as seen in Figure 5 can be selected. According to the connection style of DC-motor to be driven, again proper style of power cables for the output ports, will be selected.
For the measurement ports, the information on test procedures will be requested. Already selected ports for measurements are input and output voltages, ground connection of the motor drive. Since a series connection is requested for the electrical power calculations, it is assumed that power measurements will be taken before the input and output connections. If it is requested, the measurement ports for PWM signals of the gate drivers can be brought into the open.

To protect the components from over-voltages and over-currents during the operation, below measures can be applied to the design:

- Fuses or current sensors at both the input and output sides of the driver circuit is thought to be implemented for over-current protection. If current sensors are to be implemented on the design, some alarm signal is to be presented to the user through some led or control method can be implemented to cut the power of the circuit.
- Since we are asked to supply around 2 kW power through the motor driver (excluding losses), we are dealing with high levels of current and power that can be harmful to a human body. Therefore, proper insulation will be placed on the power lines, ports, and around the equipment.
- To cancel the parasitic effects of the non-idealities of the components, proper countermeasures will be considered.

## 3 Computer Simulations

### 3.1 LTspice Simulations

Since the 4-quadrant operation and control of the H-Bridge topology is not simple, we made comprehensive simulations using LTspice.A brief description of those and their results will be explained in this subsection. First, the simulation model will be described.

The model for the topology we are using is given in Figure 6. MOSFET models are chosen from the libraries of LTspice, whose ratings are compatible with our operation ranges. To simulate the rectified DC voltage on the input side, we occasionally used an ideal DC source to simplify the results by avoiding the input voltage ripple. We used a diode to model the one-directional current flow of the rectifier, and a capacitor to model the output filtering capacitor of the rectifier. The chopper and the H-Bridge is model is rather straightforward.


Figure 6: Simulation model for the 4-quadrant motor driver topology we choose

The controller and gate driver sections in Figure 7 are modeled using behavioral and usual voltage sources to create the necessary gate to source voltages.


Figure 7: A simple model to simulate the gate driver and controller operation

The electromechanical simulation models for DC motors are given in Figure 8. Since the simple model of the DC motor is also LTI (Linear Time Invariant), we can simulate it using the LTI circuit which is built and shown in the figure. The model can be derived using the mechanical laws for rotational systems, the torque and back emf formulas of the DC motor models, and Kirchoff’s circuital laws. The motor parameters are not the final values, but found iteratively to simulate the DC motor we used as realistically as possible. Note that another DC machine is coupled to our DC machine which is going to be the The overall model for the LTspice simulations is given in Figure 9.


Figure 8: Electromechanical simulation model for DC motors


Figure 9: The complete simulation model used for the DC motor drive simulations in LTspice

For the forward motoring region simulations, M1 and M2 MOSFETs are used for switching, M3 is always off, and M4 is always on for H-Bridge to operate as a synchronous buck converter. The output voltage level is directly proportional with the duty cycle of M1. For example, for 90% duty, we obtain 180V average voltage on the motor terminals, and we obtain 100V for 50% duty. These cases are simulated and shown in Figures 10 and
11. The current on the 16 Ω load, the armature current, and the voltage on the H-Bridge terminals are given in the figures. Note that for these values, one can supply more than 2kW power with the motor driver. Hence, current and voltage ratings of the MOSFETs can be determined using such a simulation (keeping the other practical effects in mind).


Figure 10: Forward motoring simulation for 90% duty


Figure 11: Forward motoring simulation for 50% duty

All these simulations are also done with a rectified input, which is coming from a three phase full bridge rectifier. Forward motoring simulation results for the rectified input voltage is given in Figure 12. Note that there is a significant current ripple in steady state, which is not desired. This will be avoided by the closed loop PID current control by changing the duty according to the input voltage.

The average power plots for the output of the driver and one of the switching MOS-FETs (M1) are given in Figure 13. The average power consumed by the MOSFET is also calculated and found to be around 10W. This value does not accurately model the real losses, but still gives an idea about the order of magnitude of the MOSFET losses, which is very satisfying for this simulation. In future simulations, more realistic thermal models and simulations will be made.


Figure 12: Forward motoring simulation for 90% duty with rectified input


Figure 13: Forward motoring simulation for 90% duty with rectified input, power plots

For testing both the forward motoring and regenerative breaking, we made a simulation in which we suddenly change the duty from 90% to 50%. This will try to slow down the motor and the motor will release its dissipate its kinetic energy by supplying power to the driver. At this moment, since we did not switch on the chopper resistor in the simulation, the capacitor on the input side is charged to a large value. The transient response is seen in Figure 14. Note that when our current sensor senses the reverse current, the micro-controller will switch the chopper resistor on and the energy will be dissipated on the resistor.


Figure 14: Regenerative breaking simulation for sudden slow down (transient)

The same simulations are run for the reverse motoring operation (M1 off, M2 on, M3 and M4 switched for a synchronous buck with inverted output voltage). The results were similar to the forward motoring case, except for the directions of the currents and voltages on the armature side, which was expected.

Finally, the continuous operation in the generation mode is tested by supplying a higher voltage to the other motor. In this operation, none of the MOSFETs are switched on except the chopper switch. The current flow is permitted by the body diodes of the MOSFETs. In the real case, M1 and M4 can be switched to increase the efficiency, but no need to simulate that case. Chopper MOSFET is switched on after 1ms the other motor starts to rotate. The simulation results are given in Figure 15. One can see that the armature current is negative after the transient, hence supplied to the driver; and the chopper current is positive. These are the desired transient and steady responses of the generation mode and the results are as expected.


Figure 15: Continuous generation mode simulation

In the next steps, we need to consider the inductances and resistances caused by the copper tracks of the PCB layout, which will cause unwanted effects. The realistic models of the components we choose will also be included in the simulations to get better results. Finally, thermal simulations will be conducted according to the directives given by the component manufacturers to further investigate the thermal properties of the system. We continuously update and iterate our simulations to obtain a better view of the electrical, thermal, and mechanical systems considered in our project. For now, we have seen that using H-Bridge topology, we can operate our DC motor in all 4-quadrants with great success.

### 3.2 MATLAB Simulations

Expected circuitry is simulated using MATLAB/Simulink environment. The first stage is added as a three-phase full-bridge rectifier. After that H-bridge and motor simulations are added to have a complete simulation. Simulation setup can be seen in Figures 16 & 17.


Figure 16: MATLAB Simulation Model Three-Phase FBDR.


Figure 17: MATLAB Simulation Model H-Bridge

In this simulation setup, phase-to-phase voltages are given as 150 Vrms. The output is around 200 Vrms with 20 Vpp ripple. The H-bridge and DC motor are driven with the output of a three-phase full bridge diode rectifier. Separate simulations are run for motoring, reverse motoring, and regenerative braking modes of operation. In forward motoring, the system works as a synchronous DC-DC buck converter. The output of the forward motoring can be seen in the 50 percent duty cycle in Figure 18. The output current is observed to be too much for the system. This is because there is no soft starter simulated. The control part will be implemented later.


Figure 18: H-Bridge and DC Motor Simulation at D=0.5 - Forward Motoring

In Figure 19, we see the reverse motoring graph of the motor. It is just the inverted version of forward motoring. The system works with the same logic; however, the controlled MOSFETs are changed due to change of operation.


Figure 19: H-Bridge and DC Motor Simulation at D=0.5 - Reverse Motoring

The intention of using an H-bridge is to be able to have the four-quadrant drive. More on that topic is explained in Design Decisions[2]. The other operation quadrants are braking regions. Braking is simulated in the model by adding a resistor and another MOSFET parallel to the rectifier output as in Figure 20.


Figure 20: Braking Mode Added Circuitry

In regenerative braking, the intention is usually to charge a battery system connected to the motor. We will dissipate this external motor energy using a chopper resistor. When it is in braking mode we turn on our MOSFET. More on the operation of the braking mode is explained in Design Decisions[see 2].
Figure 21 shows that the current gets below zero, which means our motor injects current into the other direction. This change in the current increases the voltage if not dissipated properly.

Figure 21: Forward Braking from duty cycle D=0.6 to D=0.3

## 4 Component Selection

### 4.1 Three-Phase Full Bridge Rectifier

In the first stage, we need a three-phase rectifier. For the three-phase rectifier, we decided to use a three-phase bridge diode similar to the [2] in Figure 22 to rectify the signal with the addition of an appropriately sized capacitor. Necessary constraints are given in the Table 1. If we struggle on the three-phase rectifier, we can also consider turning back to the single-phase version of the topology.

Peak Voltage | Peak Current | Voltage Ripple
210 Vpeak | 31A | 20Vpp

Table 1: Ratings obtained from the Simulations


Figure 22: Three-phase Full Bridge

### 4.2 MOSFET Selection

In MOSFET Selection, transients and peak values play an important role during the switching instants. For conduction modes, continuous current is considered.

Peak Voltage | Peak Current | Continuous Current
210 V | 30A | 10A

Table 2: Ratings obtained from the Simulations

As the voltage rating of the MOSFET increases, the Rds,on resistance of the MOSFET increases. We decided to keep our MOSFETs around the boundaries because we use five of them.
There was not enough time to do wide market research for the component selection. Therefore only a few models can be detected initially. Table 4 shows some of the possible options. If we can find a model that suits better to our design than the ones given in Table 4, in terms of efficiency, cost and availability, we will consider choosing that model for our design.

Peak Voltage | Peak Current | Continuous Current
300 V | 50A | 30 40A

Table 3: Intended Ratings for MOSFETS

Model | Vds Voltage(V) | Continuous Current(A) | Rds,on(mΩ) | Peak Current(A)
FDAF62N28 FDAF75N28 FDB38N30U AUIRFP4409 IXFP38N30X3 FDA38N30 IXTQ52N30P IPB60R060P7ATMA1 | 280 280 300 300 300 300 300 600 | 36 46 38 36 36 38 52 48 | 51 51 120 69 34 70 66 60 | 144 184 152 156 60A 150 150A 151A

Table 4: Some of the Selected MOSFETs

## 5 Conclusion

In this report, the first analysis of the selected design for the DC-motor drive, is performed. For the achievement of 4 quadrant operation and ease of control, full-bridge diode rectifier and H-bridge is selected as the design topology. The selected design is compared with other possible topologies for the task based on its advantages and theoretical performances. Simulation of the individual modules are done with some of the non-idealities being present in the simulations. According to the simulation results, rated voltage and current values for different modes of operations, are detected for the components to be implemented in real life application. Appropriate and commercially available diodes, MOSFETs and capacitors are selected for the implementation step of the project.
In the next steps of the project, the most suitable and commercially available ones from the selected models (also new models found recently in the further market research), will be bought. After checking the detailed simulation of these models (including non-idealities of the models to the simulation as much as possible), the implementation phase will start and considering the project specifications, design deliverables and test requirements, design will be modified until the end of the implementation phase of the project.

## References

[1] Ee463 github page. [Online]. Available: https://github.com/odtu/ee463
[2] Three-phase full bridge diode rectifier example model. [Online]. Available: https://www.motorobit.com/urun/sql50a-50a-1200v-aluminyum-3-fazli-kopru-diyot

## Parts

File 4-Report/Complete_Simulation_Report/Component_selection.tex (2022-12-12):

\section{Component Selection} \label{component}

\subsection{Three-Phase Full Bridge Rectifier}
In the first stage, we need a three-phase rectifier. For the three-phase rectifier, we decided to use a three-phase bridge diode similar to the \cite{three-phase_bridge} in Figure \ref{fig:bridge} to rectify the signal with the addition of an appropriately sized capacitor. Necessary constraints are given in the Table \ref{tab:ratings_diode}. If we struggle on the three-phase rectifier, we can also consider turning back to the single-phase version of the topology.

\begin{table}[ht]
    \centering
        \begin{tabular}{|c|c|c|}
        \hline
         Peak Voltage   & Peak Current    & Voltage Ripple  \\ 
        \hline
         210 Vpeak      & 31A             & 20Vpp           \\
        \hline
        \end{tabular}
    \caption{Ratings obtained from the Simulations}
    \label{tab:ratings_diode}
\end{table}

\begin{figure}[ht]
    \centering
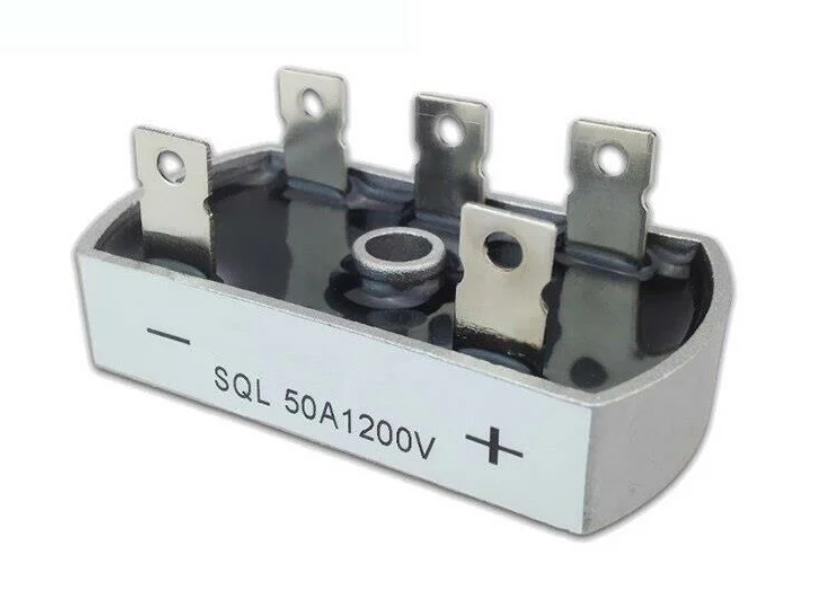
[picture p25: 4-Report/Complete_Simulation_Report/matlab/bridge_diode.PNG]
    
    \caption{Three-phase Full Bridge}
    \label{fig:bridge}
\end{figure}

\subsection{MOSFET Selection}
In MOSFET Selection, transients and peak values play an important role during the switching instants. For conduction modes, continuous current is considered.

\begin{table}[ht]
    \centering
        \begin{tabular}{|c|c|c|}
        \hline
         Peak Voltage   & Peak Current    & Continuous Current  \\
         \hline
         210 V          & 30A             & 10A          \\
        \hline
        \end{tabular}
    \caption{Ratings obtained from the Simulations}
    \label{tab:ratings_DC}
\end{table}

As the voltage rating of the MOSFET increases, the $R_{ds,on}$ resistance of the MOSFET increases. We decided to keep our MOSFETs around the boundaries because we use five of them. 

\begin{table}[ht]
    \centering
        \begin{tabular}{|c|c|c|}
        \hline
         Peak Voltage   & Peak Current    & Continuous Current  \\ 
         \hline
         300 V          & 50A          & 30~40A          \\
        \hline
        \end{tabular}
    \caption{Intended Ratings for MOSFETS}
    \label{tab:ratings_MOS}
\end{table}
There was not enough time to do wide market research for the component selection. Therefore only a few models can be detected initially. Table \ref{tab:selected_MOS} shows some of the possible options. If we can find a model that suits better to our design than the ones given in Table \ref{tab:selected_MOS}, in terms of efficiency, cost and availability, we will consider choosing that model for our design. 

\begin{table}[ht]
    \centering
        \begin{tabular}{|c|c|c|c|c|}
        \hline
         Model   & $V_{ds}$ Voltage(V)    & Continuous Current(A) & $R_{ds,on}(m\Omega)$ & Peak Current(A) \\ 
        \hline
        
         FDAF62N28       &280           &36              &51     &144\\
         FDAF75N28      &280           &46             &51      &184\\
         FDB38N30U       &300           &38             &120     &152\\
         AUIRFP4409     &300            &36             &69     &156\\
         IXFP38N30X3   & 300           & 36            & 34     & 60A\\
         FDA38N30       &300           &38             &70       &150\\ 
         IXTQ52N30P   & 300           & 52            & 66     & 150A\\
         IPB60R060P7ATMA1 &600         &48             &60       &151A\\
           
        \hline
        \end{tabular}
    \caption{Some of the Selected MOSFETs}
    \label{tab:selected_MOS}
\end{table}

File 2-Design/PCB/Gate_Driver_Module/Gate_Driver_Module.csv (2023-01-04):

Source: | C:\Users\isikemir\Desktop\Courses\EE463\TermProject\EE463-HardwareProject\2-Design\PCB\Gate_Driver_Module\Gate_Driver_Module.kicad_sch
Date: | 1/4/2023 12:27:51 AM
Tool: | Eeschema (6.0.9)
Generator: | C:\Program Files\KiCad\6.0\bin\scripting\plugins/bom_csv_grouped_by_value.py
Component Count: | 11
Individual Components:
Item | Qty | Reference(s) | Value | LibPart | Footprint | Datasheet
 |  | C1 | 4.7uF | Device:C_Polarized_Small_US | Capacitor_SMD:CP_Elec_4x5.4 | ~
 |  | C2 | 0.1uF | Device:C_Small | Capacitor_SMD:C_0805_2012Metric_Pad1.18x1.45mm_HandSolder | ~
 |  | C3 | 0.1uF | Device:C_Small | Capacitor_SMD:C_0805_2012Metric_Pad1.18x1.45mm_HandSolder | ~
 |  | J1 | Conn_01x04_Male | Connector:Conn_01x04_Male | Connector_PinHeader_2.54mm:PinHeader_1x04_P2.54mm_Vertical | ~
 |  | J2 | Conn_01x04_Male | Connector:Conn_01x04_Male | Connector_PinHeader_2.54mm:PinHeader_1x04_P2.54mm_Vertical | ~
 |  | R1 | 470-330-220-100R | Device:R_Small_US | Resistor_SMD:R_0805_2012Metric_Pad1.20x1.40mm_HandSolder | ~
 |  | R2 | 680-470-330-220R | Device:R_Small_US | Resistor_SMD:R_0805_2012Metric_Pad1.20x1.40mm_HandSolder | ~
 |  | R3 | 1kR, 0.25W | Device:R_Small_US | Resistor_SMD:R_0805_2012Metric_Pad1.20x1.40mm_HandSolder | ~
 |  | U1 | ROE-0512S | ee463_symbol_library:ROE-0512S | ee463_footprint_lib:ROE-0512S
 |  | U2 | LTV-817 | Isolator:LTV-817 | Package_DIP:SMDIP-4_W7.62mm | http://www.us.liteon.com/downloads/LTV-817-827-847.PDF
 |  | U3 | TC4421A | Driver_FET:TC4421 | Package_SO:SOIC-8_3.9x4.9mm_P1.27mm | http://ww1.microchip.com/downloads/en/DeviceDoc/20001420F.pdf
Collated Components:
Item | Qty | Reference(s) | Value | LibPart | Footprint | Datasheet
1 | 1 | C1 | 4.7uF | Device:C_Polarized_Small_US | Capacitor_SMD:CP_Elec_4x5.4 | ~
2 | 2 | C2, C3 | 0.1uF | Device:C_Small | Capacitor_SMD:C_0805_2012Metric_Pad1.18x1.45mm_HandSolder | ~
3 | 2 | J1, J2 | Conn_01x04_Male | Connector:Conn_01x04_Male | Connector_PinHeader_2.54mm:PinHeader_1x04_P2.54mm_Vertical | ~
4 | 1 | R1 | 470-330-220-100R | Device:R_Small_US | Resistor_SMD:R_0805_2012Metric_Pad1.20x1.40mm_HandSolder | ~
5 | 1 | R2 | 680-470-330-220R | Device:R_Small_US | Resistor_SMD:R_0805_2012Metric_Pad1.20x1.40mm_HandSolder | ~
6 | 1 | R3 | 1kR, 0.25W | Device:R_Small_US | Resistor_SMD:R_0805_2012Metric_Pad1.20x1.40mm_HandSolder | ~
7 | 1 | U1 | ROE-0512S | ee463_symbol_library:ROE-0512S | ee463_footprint_lib:ROE-0512S
8 | 1 | U2 | LTV-817 | Isolator:LTV-817 | Package_DIP:SMDIP-4_W7.62mm | http://www.us.liteon.com/downloads/LTV-817-827-847.PDF
9 | 1 | U3 | TC4421A | Driver_FET:TC4421 | Package_SO:SOIC-8_3.9x4.9mm_P1.27mm | http://ww1.microchip.com/downloads/en/DeviceDoc/20001420F.pdf

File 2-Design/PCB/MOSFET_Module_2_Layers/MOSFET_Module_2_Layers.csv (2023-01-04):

Source: | C:\Users\isikemir\Desktop\Courses\EE463\TermProject\EE463-HardwareProject\2-Design\PCB\MOSFET_Module_2_Layers\MOSFET_Module_2_Layers.kicad_sch
Date: | 1/4/2023 12:19:16 AM
Tool: | Eeschema (6.0.9)
Generator: | C:\Program Files\KiCad\6.0\bin\scripting\plugins/bom_csv_grouped_by_value.py
Component Count: | 14
Individual Components:
Item | Qty | Reference(s) | Value | LibPart | Footprint | Datasheet
 |  | C1 | 1uF | Device:C_Small | Capacitor_SMD:C_1210_3225Metric_Pad1.33x2.70mm_HandSolder | ~
 |  | C2 | 1uF | Device:C_Small | Capacitor_SMD:C_1210_3225Metric_Pad1.33x2.70mm_HandSolder | ~
 |  | C3 | 1uF | Device:C_Small | Capacitor_SMD:C_1210_3225Metric_Pad1.33x2.70mm_HandSolder | ~
 |  | C4 | 1uF | Device:C_Small | Capacitor_SMD:C_1210_3225Metric_Pad1.33x2.70mm_HandSolder | ~
 |  | D1 | D_Zener | Device:D_Zener | Diode_SMD:D_SOD-123 | ~
 |  | D2 | D_Zener | Device:D_Zener | Diode_SMD:D_SOD-123 | ~
 |  | J1 | Conn_01x04_Male | Connector:Conn_01x04_Male | Connector_PinHeader_2.54mm:PinHeader_1x04_P2.54mm_Horizontal | ~
 |  | J2 | Conn_01x04_Male | Connector:Conn_01x04_Male | Connector_PinHeader_2.54mm:PinHeader_1x04_P2.54mm_Horizontal | ~
 |  | Q1 | SPW47N60 | Device:Q_NMOS_GDS | ee463_footprint_lib:TO-247-3_Horizontal_TabDown_ee463 | ~
 |  | Q2 | SPW47N60 | Device:Q_NMOS_GDS | ee463_footprint_lib:TO-247-3_Horizontal_TabDown_ee463 | ~
 |  | R1 | 22-10-5R | Device:R_Small_US | Resistor_SMD:R_0805_2012Metric_Pad1.20x1.40mm_HandSolder | ~
 |  | R2 | 22-10-5R | Device:R_Small_US | Resistor_SMD:R_0805_2012Metric_Pad1.20x1.40mm_HandSolder | ~
 |  | R3 | 10kR | Device:R_Small_US | Resistor_SMD:R_0805_2012Metric_Pad1.20x1.40mm_HandSolder | ~
 |  | R4 | 10kR | Device:R_Small_US | Resistor_SMD:R_0805_2012Metric_Pad1.20x1.40mm_HandSolder | ~
Collated Components:
Item | Qty | Reference(s) | Value | LibPart | Footprint | Datasheet
1 | 4 | C1, C2, C3, C4 | 1uF | Device:C_Small | Capacitor_SMD:C_1210_3225Metric_Pad1.33x2.70mm_HandSolder | ~
2 | 2 | D1, D2 | D_Zener | Device:D_Zener | Diode_SMD:D_SOD-123 | ~
3 | 2 | J1, J2 | Conn_01x04_Male | Connector:Conn_01x04_Male | Connector_PinHeader_2.54mm:PinHeader_1x04_P2.54mm_Horizontal | ~
4 | 2 | Q1, Q2 | SPW47N60 | Device:Q_NMOS_GDS | ee463_footprint_lib:TO-247-3_Horizontal_TabDown_ee463 | ~
5 | 2 | R1, R2 | 22-10-5R | Device:R_Small_US | Resistor_SMD:R_0805_2012Metric_Pad1.20x1.40mm_HandSolder | ~
6 | 2 | R3, R4 | 10kR | Device:R_Small_US | Resistor_SMD:R_0805_2012Metric_Pad1.20x1.40mm_HandSolder | ~

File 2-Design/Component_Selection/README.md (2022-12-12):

## Feedback Session Presentation

Google Slides presentation link for the Feedback Session is given [here](https://docs.google.com/presentation/d/1oQX1AL4118MGG43J7JtUT8aee3LiUoVbpQ-Jl7rUWLI/edit?usp=sharing).

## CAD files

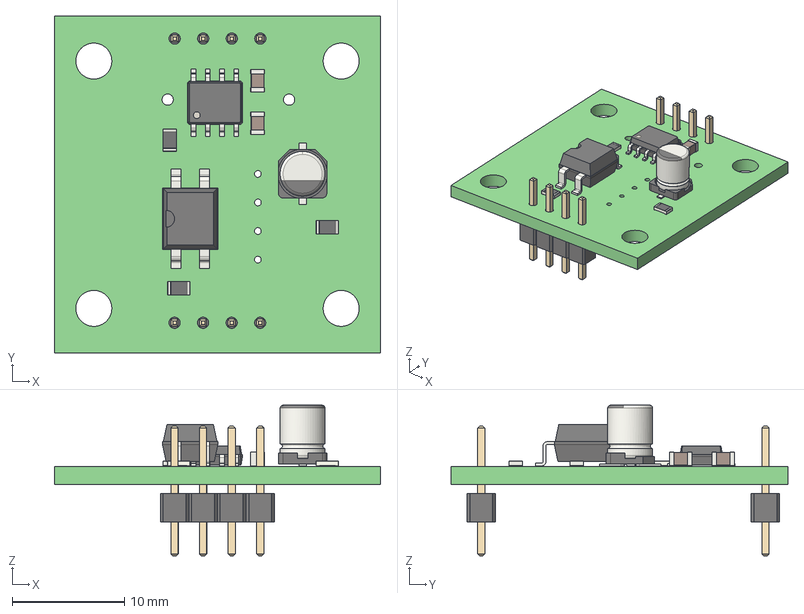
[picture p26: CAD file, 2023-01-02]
2-Design/PCB/Gate_Driver_Module/Gate_Driver_Module.step
29.0 x 30.0 x 13.4 mm
Gate_Driver_Module PCB

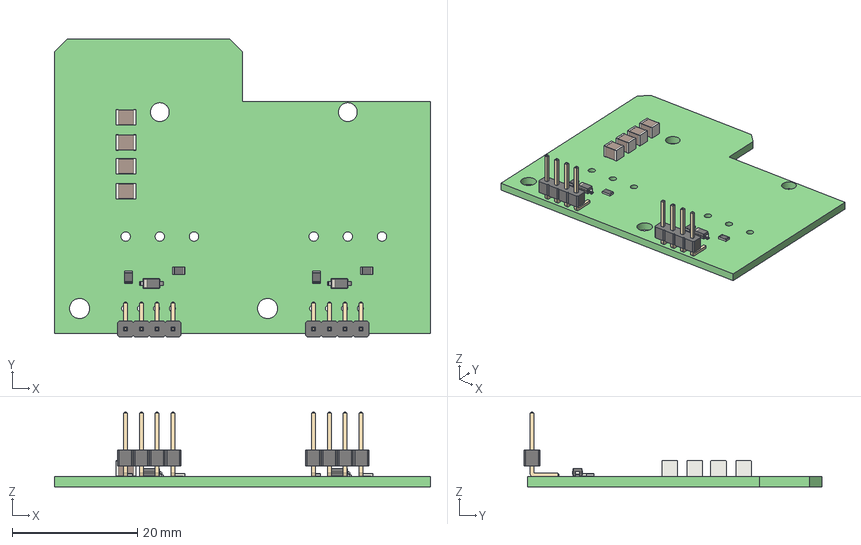
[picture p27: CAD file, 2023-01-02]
2-Design/PCB/MOSFET_Module_2_Layers/MOSFET_Module_2_Layers.step
60.0 x 47.5 x 11.9 mm
MOSFET_Module_2_Layers PCB

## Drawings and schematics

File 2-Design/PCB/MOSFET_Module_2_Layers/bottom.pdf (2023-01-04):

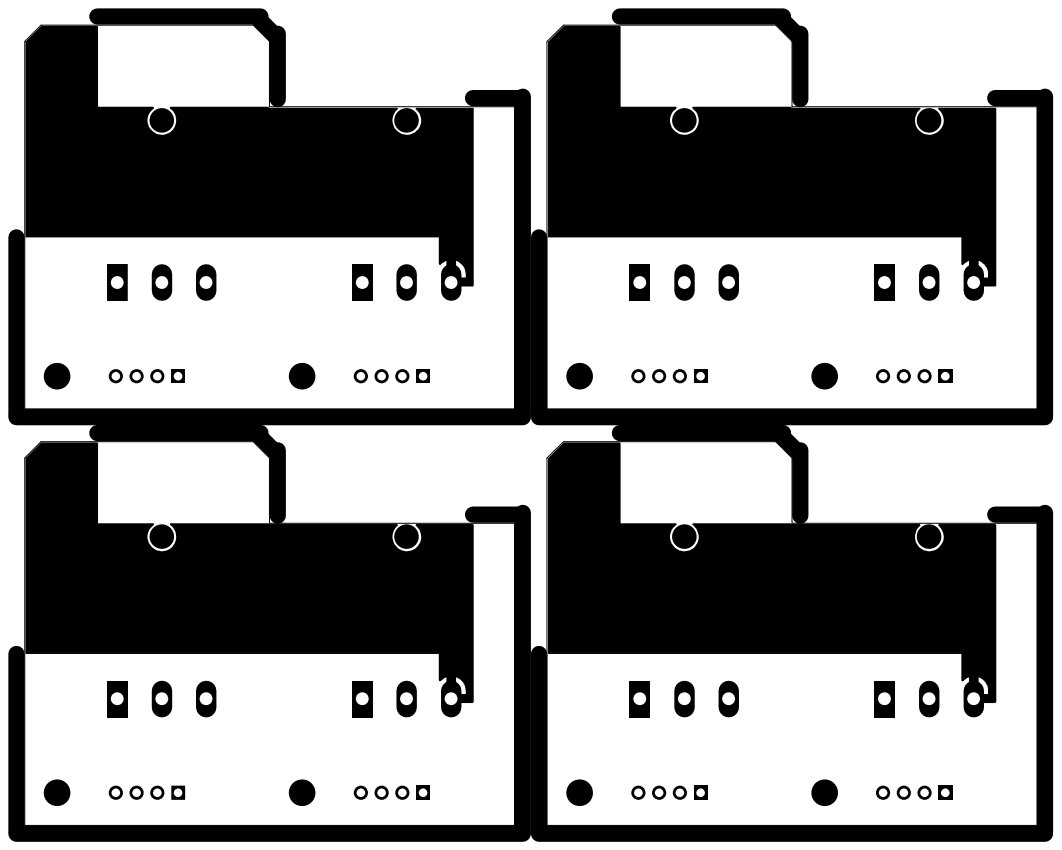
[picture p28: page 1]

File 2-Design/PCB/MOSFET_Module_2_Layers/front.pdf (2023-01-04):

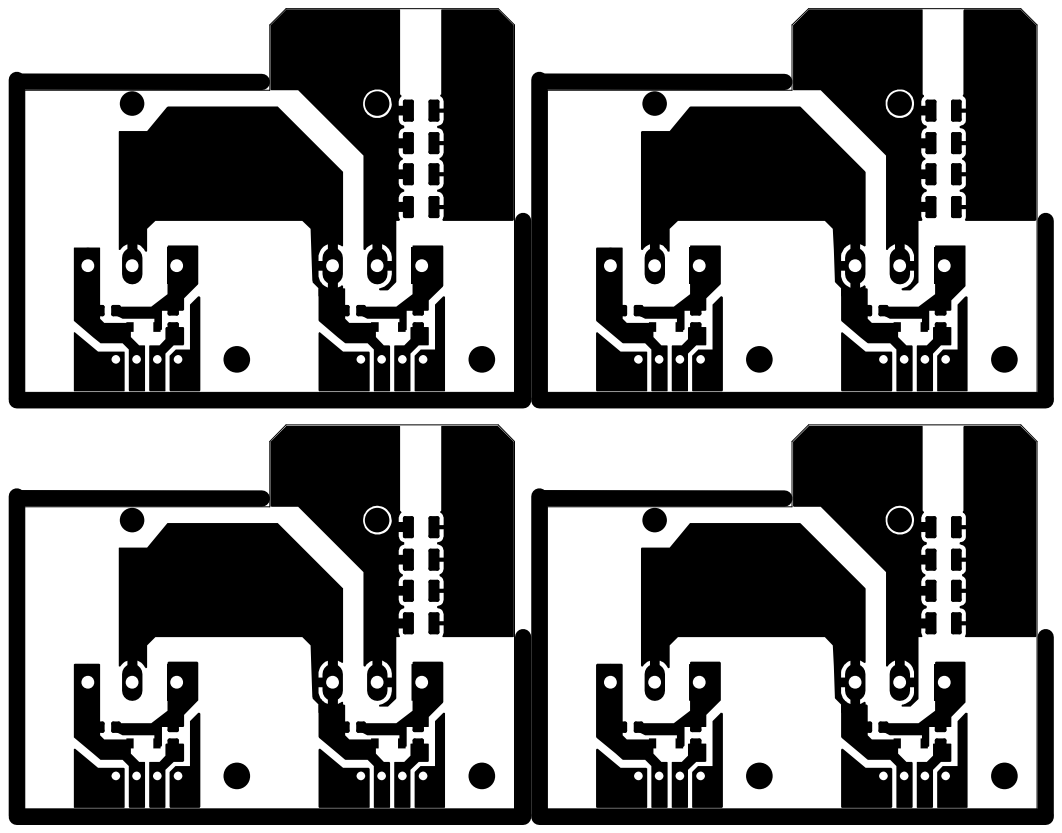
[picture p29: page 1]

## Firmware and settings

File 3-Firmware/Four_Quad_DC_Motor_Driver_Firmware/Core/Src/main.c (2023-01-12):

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
/* Includes ------------------------------------------------------------------*/
#include "main.h"

ADC_HandleTypeDef hadc1;
ADC_HandleTypeDef hadc2;
DMA_HandleTypeDef hdma_adc1;

TIM_HandleTypeDef htim1;
TIM_HandleTypeDef htim4;

/* USER CODE BEGIN PV */

// Define PID parameters
uint32_t Kp = 50;
uint32_t Kd = 0;
uint32_t Ki = 0;
float delta_t = 1/72000; // Control loop period, must be equal to TIM4 interrupt frequency (72KHz)

// Define the variables to store input values
float I_sense = 0;	// Measured armature current
float I_set = 0;  // Set value for armature current
float I_set_av = 0; // Set value moving average
float I_set_temp = 0; // Defined for calculation purposes
uint32_t Gen_mode = 0; // Generator mode boolean (active low)
uint32_t Soft_st = 0;  // Latching soft start
uint32_t Soft_st_done = 0; // Enable if the motor is already started
uint32_t forward = 1;  // 1 for forward motoring, 0 for reverse motoring

// Define duty variable
uint32_t duty = 0; // will be written to TIM1->CCR1 & TIM1->CCR2

// Average Buffers
uint16_t adc_buf_set[ADC_AVE_SAMPLE];
uint16_t adc_buf_sense[ADC_AVE_SAMPLE];

/* USER CODE END PV */

void SystemClock_Config(void);
static void MX_GPIO_Init(void);
static void MX_DMA_Init(void);
static void MX_TIM1_Init(void);
static void MX_ADC1_Init(void);
static void MX_TIM4_Init(void);
static void MX_ADC2_Init(void);
/* USER CODE BEGIN PFP */
uint16_t ADC1_Read();
uint16_t ADC2_Read();
/* USER CODE END PFP */

/**
  * @brief  The application entry point.
  * @retval int
  */
int main(void)
{
  /* MCU Configuration--------------------------------------------------------*/

  /* Reset of all peripherals, Initializes the Flash interface and the Systick. */
  HAL_Init();

  /* Configure the system clock */
  SystemClock_Config();

  /* Initialize all configured peripherals */
  MX_GPIO_Init();
  MX_DMA_Init();
  MX_TIM1_Init();
  MX_ADC1_Init();
  MX_TIM4_Init();
  MX_ADC2_Init();
  /* USER CODE BEGIN 2 */
  HAL_TIM_Base_Start_IT(&htim4);

  for(int j=0;j<ADC_AVE_SAMPLE;j++){
  	adc_buf_set[j] = 2048;
  	adc_buf_sense[j] =2048;
  }


  HAL_Delay(1000); // Wait a second

  // HAL_TIM_Base_Start_IT(&htim1);
  HAL_TIM_PWM_Start(&htim1, TIM_CHANNEL_1);
  HAL_TIMEx_PWMN_Start(&htim1, TIM_CHANNEL_1);
  HAL_TIM_PWM_Start(&htim1, TIM_CHANNEL_2);
  HAL_TIMEx_PWMN_Start(&htim1, TIM_CHANNEL_2);
  HAL_TIM_PWM_Start(&htim1, TIM_CHANNEL_3);
  HAL_TIMEx_PWMN_Start(&htim1, TIM_CHANNEL_3);


  /* USER CODE END 2 */

  /* Infinite loop */
  /* USER CODE BEGIN WHILE */
  while (1)
  {
    /* USER CODE END WHILE */

    /* USER CODE BEGIN 3 */
  }
  /* USER CODE END 3 */
}

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
/* USER CODE BEGIN 4 */

uint16_t ADC1_Read()
{
	// Get ADC value
	HAL_ADC_Start(&hadc1);
	HAL_ADC_PollForConversion(&hadc1, HAL_MAX_DELAY);


	return HAL_ADC_GetValue(&hadc1);
}
uint16_t ADC2_Read()
{
	// Get ADC value
	HAL_ADC_Start(&hadc2);
	HAL_ADC_PollForConversion(&hadc2, HAL_MAX_DELAY);

	return HAL_ADC_GetValue(&hadc2);
}

/* USER CODE END 4 */
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


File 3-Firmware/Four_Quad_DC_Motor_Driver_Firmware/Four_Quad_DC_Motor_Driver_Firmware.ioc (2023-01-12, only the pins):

Mcu.UserName=STM32F103C8Tx
PA0-WKUP.GPIO_Label=I_SET
PA0-WKUP.Signal=ADCx_IN0
PA1.GPIO_Label=I_SENSE
PA1.Signal=ADCx_IN1
PA10.GPIO_Label=PWM5
PA10.Signal=S_TIM1_CH3
PA13.Signal=SYS_JTMS-SWDIO
PA14.Signal=SYS_JTCK-SWCLK
PA2.GPIO_Label=SOFT_ST
PA2.Signal=GPXTI2
PA3.GPIO_Label=GEN_MODE
PA3.Signal=GPIO_Input
PA4.GPIO_Label=GPIO_IN_D
PA4.Signal=GPIO_Input
PA5.GPIO_Label=GPIO_OUT_D
PA5.Signal=GPIO_Output
PA8.GPIO_Label=PWM1
PA8.Signal=S_TIM1_CH1
PA9.GPIO_Label=PWM3
PA9.Signal=S_TIM1_CH2
PB13.GPIO_Label=PWM2
PB13.Signal=TIM1_CH1N
PB14.GPIO_Label=PWM4
PB14.Signal=TIM1_CH2N
PB15.GPIO_Label=PWM6
PB15.Signal=TIM1_CH3N
PD0-OSC_IN.Signal=RCC_OSC_IN
PD1-OSC_OUT.Signal=RCC_OSC_OUT

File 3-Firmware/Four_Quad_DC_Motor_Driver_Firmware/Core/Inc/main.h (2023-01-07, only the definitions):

#define internal_clock 72000000 // Internal clock is configured to 72MHz
#define ADC_BUF_LEN 4096
#define START_THRESHOLD 512
#define START_COUNT_MAX 72000*5 // 5 seconds soft start
#define ADC_AVE_SAMPLE 100
#define I_SET_Pin GPIO_PIN_0
#define I_SET_GPIO_Port GPIOA
#define I_SENSE_Pin GPIO_PIN_1
#define I_SENSE_GPIO_Port GPIOA
#define SOFT_ST_Pin GPIO_PIN_2
#define SOFT_ST_GPIO_Port GPIOA
#define SOFT_ST_EXTI_IRQn EXTI2_IRQn
#define GEN_MODE_Pin GPIO_PIN_3
#define GEN_MODE_GPIO_Port GPIOA
#define GPIO_IN_D_Pin GPIO_PIN_4
#define GPIO_IN_D_GPIO_Port GPIOA
#define GPIO_OUT_D_Pin GPIO_PIN_5
#define GPIO_OUT_D_GPIO_Port GPIOA
#define PWM2_Pin GPIO_PIN_13
#define PWM2_GPIO_Port GPIOB
#define PWM4_Pin GPIO_PIN_14
#define PWM4_GPIO_Port GPIOB
#define PWM6_Pin GPIO_PIN_15
#define PWM6_GPIO_Port GPIOB
#define PWM1_Pin GPIO_PIN_8
#define PWM1_GPIO_Port GPIOA
#define PWM3_Pin GPIO_PIN_9
#define PWM3_GPIO_Port GPIOA
#define PWM5_Pin GPIO_PIN_10
#define PWM5_GPIO_Port GPIOA

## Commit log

2022-12-01 H bridge synchronous buck successful
2022-12-04 Motor_Modelling.asc completed with a somewhat realistic motor model (special thanks to ozgurgulsuna)
2022-12-05 Reverse_Motoring.asc added, Regenerative_Breaking.asc initialized, wrong motor parameters revised
2022-12-09 Added the reverse motoring simulation
2022-12-20 KiCAD project initiated
    [Controller.kicad_sch, Converters.kicad_sch, Driver.kicad_sch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]
2022-12-20 Added the SQL50 symbol and footprint
    [Converters.kicad_sch, Four_Quad_DC_Motor_Drive.kicad_sch]
2022-12-20 Added some more schematic symbols and three phase rectifier schematics
    [Converters.kicad_sch, Four_Quad_DC_Motor_Drive.kicad_sch, Terminals.kicad_sch]
2022-12-21 Changed the driver schematic, and added some schematic symbols
    [Controller.kicad_sch, Converters.kicad_sch, Driver.kicad_sch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]
2022-12-22 Added the gate driver schematics and converter schematics
    [Converters.kicad_sch, Driver.kicad_sch, Four_Quad_DC_Motor_Drive.kicad_sch]
2022-12-22 Added the label and gate drive resistances
    [Controller.kicad_sch, Converters.kicad_sch, Driver.kicad_sch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]
2022-12-27 Gate driver changed, plus other rearrangements on the schematics
    [Controller.kicad_sch, Converters.kicad_sch, Driver.kicad_sch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]
2022-12-27 Gate drivers finished, controller pins to be arranged
    [Converters.kicad_sch, Driver.kicad_sch, Four_Quad_DC_Motor_Drive.kicad_sch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]
2022-12-29 Random Checkpoint
    [Controller.kicad_sch, Converters.kicad_sch, Four_Quad_DC_Motor_Drive.kicad_sch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]
2022-12-31 MOSFET_Module PCB v1 completed
    [MOSFET_Module.kicad_pcb, MOSFET_Module.kicad_sch]
2022-12-31 MOSFET_Module PCB v2 completed, we will call it a 1/3 day
    [Gate_Driver_Module.kicad_pcb, Gate_Driver_Module.kicad_sch, MOSFET_Module_2_Layers.kicad_pcb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]
2022-12-31 Gate Driver Module placements somewhat ready, to be drawn
    [Gate_Driver_Module.kicad_pcb, Gate_Driver_Module.kicad_sch]
2022-12-31 Gate Driver Module placements are not somewhat ready, but it takes time for isik to learn
    [Gate_Driver_Module.kicad_pcb, Gate_Driver_Module.kicad_sch]
2023-01-01 Gate Driver Module v1 completed, minor polishing to be done
    [Gate_Driver_Module.kicad_pcb, Gate_Driver_Module.kicad_sch]
2023-01-01 Gate Driver Module v1 completed
    [Gate_Driver_Module.kicad_pcb]
2023-01-02 Controller Module v1, tracks to be drawn
    [Controller_Module.kicad_pcb, Controller_Module.kicad_sch, Gate_Driver_Module.kicad_pcb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]
2023-01-02 Gate Driver Module minimum load for boost, plus Controller Module advancements
    [Controller_Module.kicad_pcb, Controller_Module.kicad_sch, Gate_Driver_Module.kicad_pcb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]
2023-01-02 Added 3d model
    [Gate_Driver_Module.step]
2023-01-02 3d models added
    [Gate_Driver_Module.step, MOSFET_Module_2_Layers.step]
2023-01-02 Controller footprint corrected
    [Controller_Module.kicad_pcb]
2023-01-03 Some changes i dont even remember
    [Controller_Module.kicad_pcb, Controller_Module.kicad_sch, Gate_Driver_Module.csv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]
2023-01-04 Firmware initialization correctedd, PWM module with dead times tested
    [Four_Quad_Firmware Debug.cfg]
2023-01-05 Controller Module Completed
    [Controller_Module.kicad_pcb, Controller_Module.kicad_sch, Four_Quad_DC_Motor_Driver_Firmware Debug.cfg]
2023-01-09 The code is simplified to operate only in forward and reverse motoring, without closed loop control
    [Four_Quad_DC_Motor_Driver_Firmware.ioc, main.c]
2023-01-12 Dead time generation problem is solved
    [Four_Quad_DC_Motor_Driver_Firmware.ioc, main.c]
2023-01-12 Initialization must be done initially, and now our MOSFETs are safe. Power isi gonul isi

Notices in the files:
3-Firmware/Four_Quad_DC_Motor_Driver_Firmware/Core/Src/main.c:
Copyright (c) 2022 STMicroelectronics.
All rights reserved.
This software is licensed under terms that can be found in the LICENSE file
